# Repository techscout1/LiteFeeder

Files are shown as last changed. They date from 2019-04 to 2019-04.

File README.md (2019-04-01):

# LiteFeeder
LiteFeeder is a extension to [LiteSolder](https://github.com/Carinalo93/LiteSolder) and [LitePlacer](https://github.com/jkuusama/LitePlacer-DEV). - Its a simple platform to start you PCBs fabrication right from your desk, without spending thousands of dollars.

# Priciple

The LiteFeeder is an automatic SMT part feeder for standard 8mm tapes. It comes with a strong magnet and a powerrail to simply mount and exchange the feeder in front of the LitePlacer. Its driven by a cheap stepper motor. The main working principle is very simple. When the LitePlacer picks a part from the LiteFeeder. The Feeder can recognize this in two ways. We used a light barrier to detect the nozzle. Futhermore in the pcb is a place for an hall sensor too. We just used the light barrier but it can be extend to both sensors by default. After detecting the nozzle the LitePlacer wait 6 seconds. After it the stepper pulls the masking tape until the next hole is detected. Thats it its. Simple but powerful! 

# Bill of materials

1x 28byj-48 Stepper Motor

1x 30x4mm Neodym Magnet

1x Red 90° right angled SMD LED

1x Green 90° right angled SMD LED

1x Right angled push switch KSS231G

1x ATtiny84 SOIC 14

1x ULN2003A SOIC 16

1x QRE1113 light barrier oder DRV5023 for nozzle dection

1x SX1106 fork light barrier for hole dection

1x JST B5B XH A Connector for the stepper

1x 9155 AVX 2 Pin Battery Connector

2x 3,5x16 Screws 

Some standard 0603 resistors, pinheader and condensators i.e. 10k or 330

# 3D parts
Housing:

[.stl](https://github.com/techscout1/LiteFeeder/blob/master/Housing.stl) [.step](https://github.com/techscout1/LiteFeeder/blob/master/Housing.stp) [.ipt](https://github.com/techscout1/LiteFeeder/blob/master/Housing.ipt)

Pulling Wheel:

[.stl](https://github.com/techscout1/LiteFeeder/blob/master/PullingWheel.stl) [.step](https://github.com/techscout1/LiteFeeder/blob/master/PullingWheel.stp) [.ipt](https://github.com/techscout1/LiteFeeder/blob/master/PullingWheel.ipt)

Powerrail: (from a pcb copper plate)

[.step](https://github.com/techscout1/LiteFeeder/blob/master/PowerRail.stp) [.ipt](https://github.com/techscout1/LiteFeeder/blob/master/PowerRail.ipt)

# PCB
We've orded the PCB at PCBway.com its really cheap an fast.
*Please Note*: the wiring diagram is fine but there are some issues with the boardlayout. Please verify it. --> You should add an 0.1µ condensator between VCC and GND otherwise it will not work fine. Futhermore the footprint of the battery connector to the powerrail must be integrated. In the gerber file is the battery footprint integrated but not the 0.1µ capacitor. 

[PCB Parts & Files](https://github.com/techscout1/LiteFeeder/blob/master/Feeder0.95.zip)

# Programm

[Software LiteFeeder](https://github.com/techscout1/LiteFeeder/blob/master/LiteFeeder_V1.zip)

Since Arduino coding on MCUs is quite simple. We uploaded our sketch. To programm we used the an Arduino Uno as ISP and the ATtinyCore for the boards manager. You can download it [here](https://github.com/SpenceKonde/ATTinyCore).

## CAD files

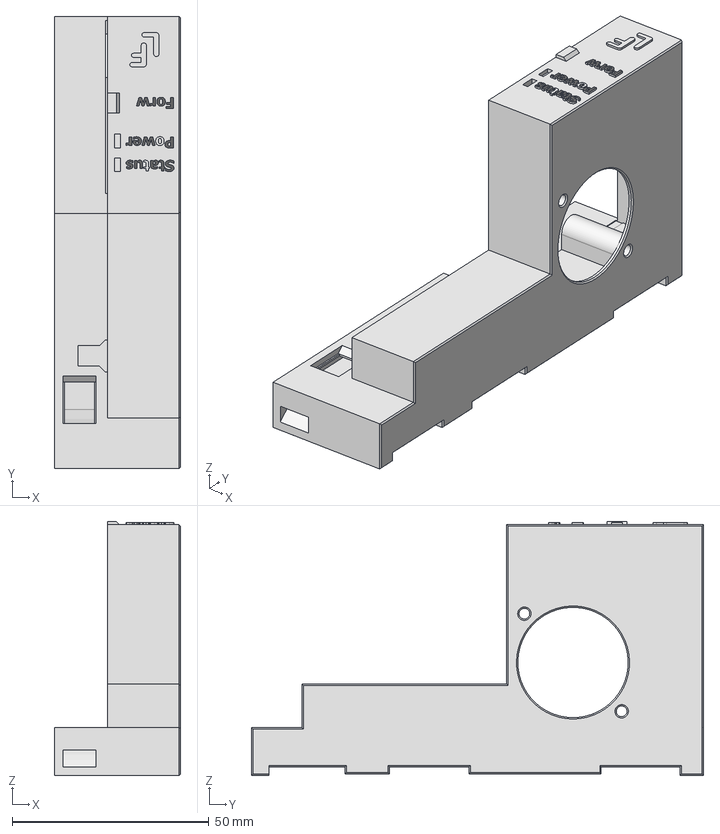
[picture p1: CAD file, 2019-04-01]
Housing.stp
32.0 x 114.8 x 64.5 mm

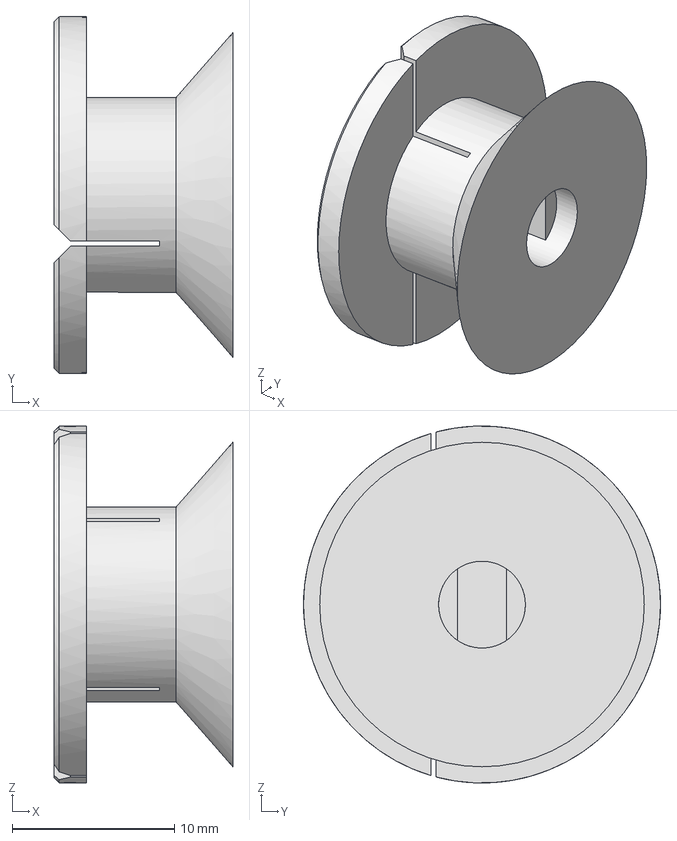
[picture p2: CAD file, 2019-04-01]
PullingWheel.stp
11.0 x 22.0 x 22.0 mm

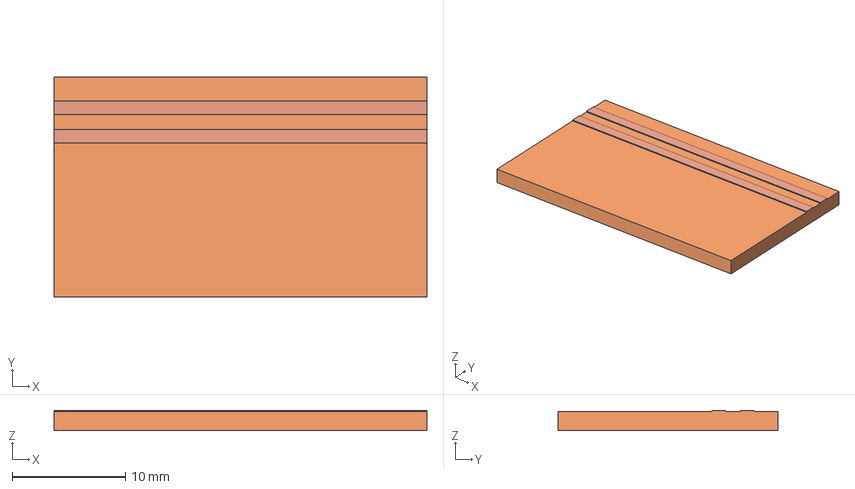
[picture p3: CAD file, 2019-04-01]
PowerRail.stp
33.0 x 19.5 x 1.80 mm

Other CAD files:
Housing.ipt
Housing.stl
PowerRail.ipt
PullingWheel.ipt
PullingWheel.stl

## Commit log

2019-04-01 Feeder latest, but with issus in the boards layout
2019-04-01 3D Parts
    [Housing.ipt, Housing.stl, Housing.stp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]
